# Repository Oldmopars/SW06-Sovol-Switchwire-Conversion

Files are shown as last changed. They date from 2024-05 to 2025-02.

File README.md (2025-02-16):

SV06 Switchwire Conversion Final Basic Enclosed
SV06 Switchwire Conversion Basic Open
SV06 Switchwire Conversion Full Monty
# SW06-Sovol-Switchwire-Conversion
Here it is. Until I can come up with a better name, I am calling it the SW06 (Switchwire/SV06). 
I had a few goals with this build. 
To reuse as many as possible of the original SV06 parts. At this point nearly all of the hard parts and electronics are being used, including the frame. Nearly all the plastic injection molded parts are replaced with printed parts. 
I wanted to make it better, faster and eliminate the Z banding issues. That is why the 		   CoreXZ. However, per the first goal, I am reusing the now unused X axis motor and putting it in the Y axis to have 2 Y axis motors. More power, and shorter belt path between motors. 
I wanted to be able to enclose it, but not require anything super complex to do so. I want to print ABS/ASA and other high temp filaments. This is one of the main reasons to base it off the Switchwire. Premade SW panel kit fits, it was designed around it. The only panel that will not fit is the deck panel, and it is now 3D printed in 6 parts to fit the SV06 print area. 
Easy upgrade path to an even better or faster machine. All of the Voron compatible toolheads including the Stealth Burner, XOL2, Dragon Burner, etc. will fit this now as it uses the Voron Mount system. This also means you can use TAP R8, CNC Tap, Beacon, Eddy, Klicky, etc. 
A budget to fit any wallet. There are 3 main options. First one is the Basic. This uses the stock 8mm Rods and LM8UU bearings in the Z, only requires 1 MGN12 linear rail. You will also need some F695 bearings, new belts and some hardware. If you do not have a RPi or some other Klipper screen, you will need that to convert to Klipper. This will keep the spend under $100 and reuse the stock hot end. 
If you can afford more, the enclosure is next. This will be a bit under $100. So, the basic, plus enclosure will cost between $150-200. 
The Full Monty. Here you add the MGN12 rails in the Z axis to full SW configuration. Add a Voron Tool Head with any upgrades you want. Add your choice of Probe, LEDs, MIC6 bed, and maybe even MGN12 for the bed.  Want to add a filter? Heater? Camera? 48mm motors? 48V with TMC5160’s? Sky is the limit and many of the options from the Switchwire will directly work on this. 
 I am still cleaning up the CAD files. Due to using the Voron as a base, moving fasteners around has been a royal pain, so most of the fasteners are not shown. I will be working to add these all in, but it will take time. 
  If anyone would like to build a BETA version, let me know and I will share the files with you. I would love to have some others build it first and help me flush out any issues I may have overlooked. 
  I look forward to sharing this with you all and hope to see many of these printers converted and doing great things. 

Please keep in mind that this is a ALPHA. I have yet to convert a full printer and so much of this is untested. Please feel free to use these files and let me know if anything needs to be fixed or changed. I would love to get feedback and see your builds. 

May 9 2024
I have updated the file. I have added the missing hardware and made some other changes. Please let me know if you find any issue with it. 

Feb 15 2025
I made some major upgrades to the X and Z motor mounts. It is now using the original Voron Switchwire motor mounts. This makes maintenace much easier. Prior version was difficult to change belt tension, or any other work on the motors. Now it is much easier to work on.

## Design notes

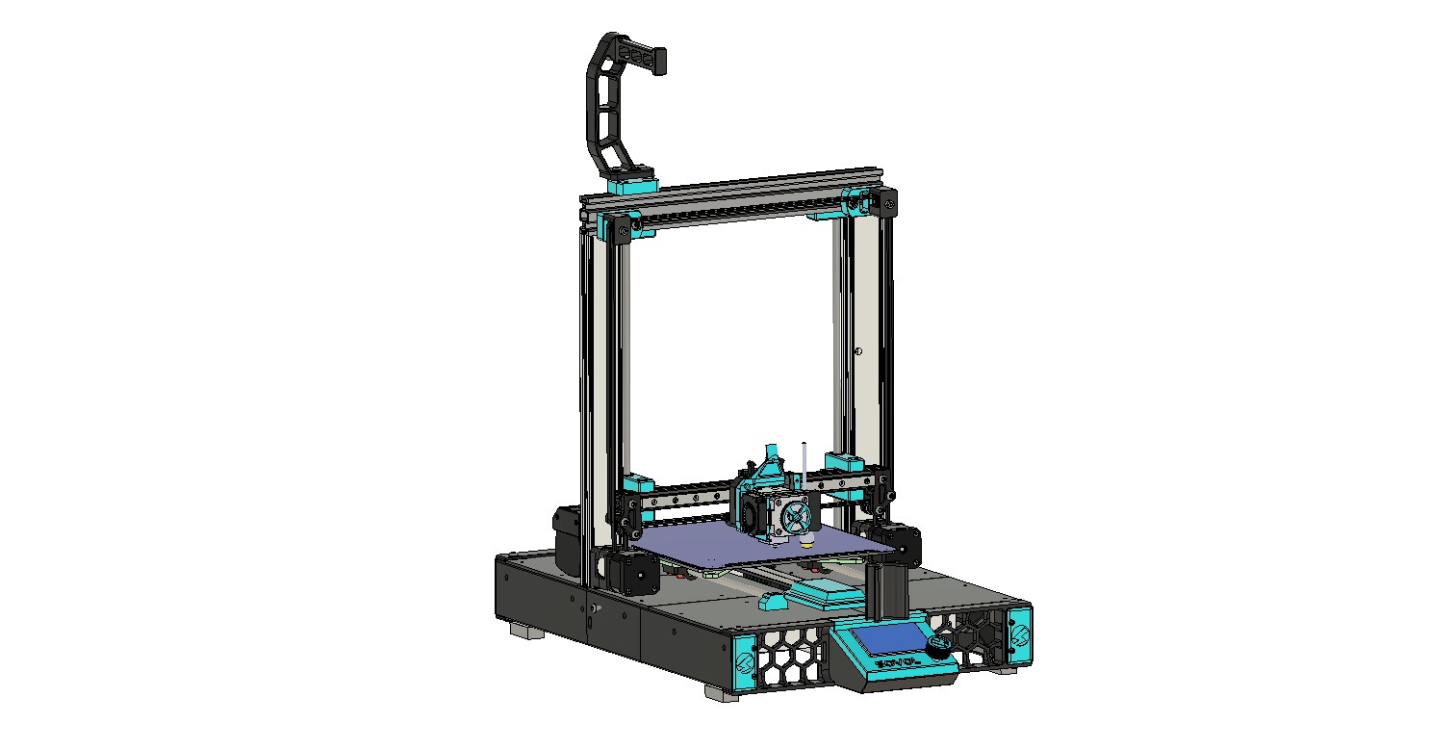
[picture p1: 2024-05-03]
SV06 Switchwire Conversion Basic Open.png

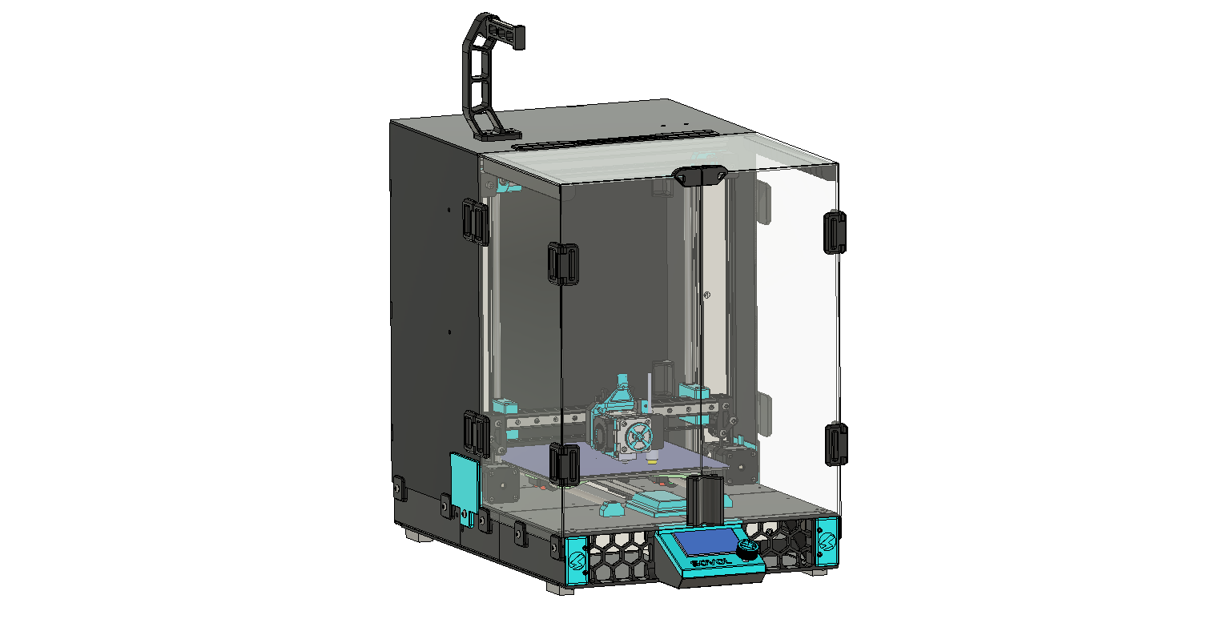
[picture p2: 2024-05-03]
SV06 Switchwire Conversion Final Basic Enclosed.png

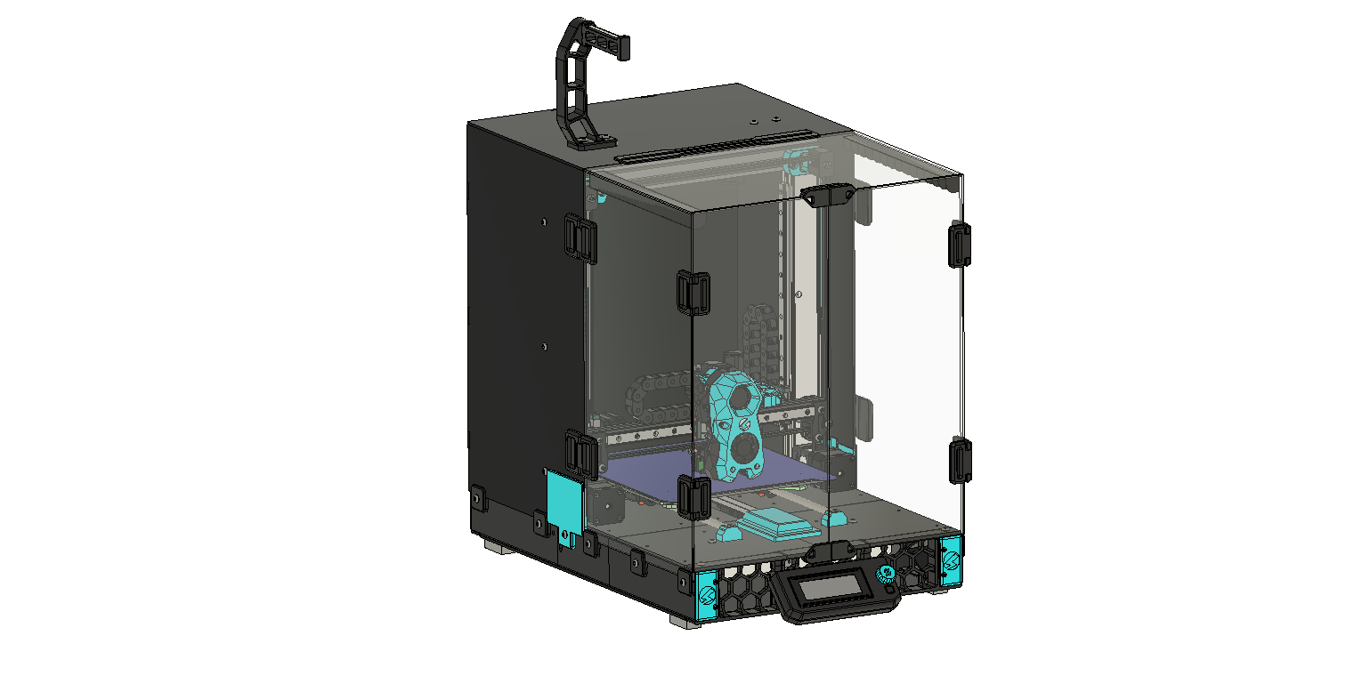
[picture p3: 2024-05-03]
SV06 Switchwire Conversion Full Monty.png

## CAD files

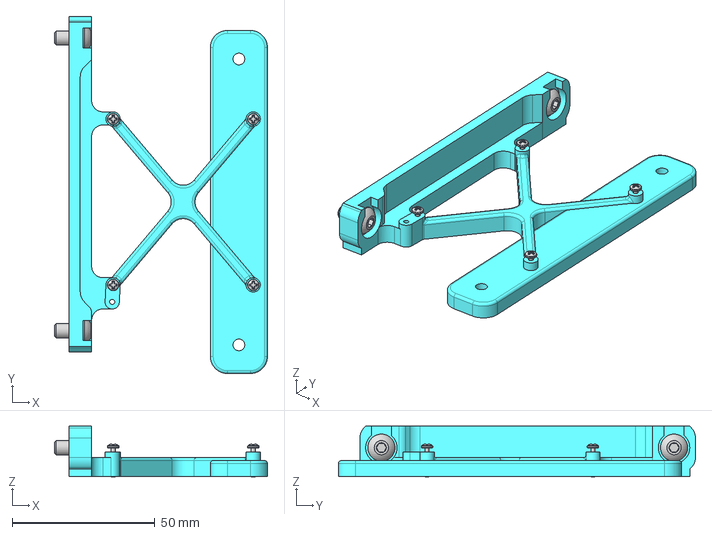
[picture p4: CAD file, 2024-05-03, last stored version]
SV06 Switchwire Conversion v7.step
74.5 x 124.9 x 17.7 mm
M5x10 BHCS (13) x 2
M2x10 SCREW x 4

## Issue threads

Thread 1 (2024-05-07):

Incomplete STEP

tt1pjm, 2024-05-07:
Not sure if it's intentional but the step only contains the RPi mount. Would be great to see the full model.

Oldmopars, 2024-05-07:
Sorry, fixing that now

Oldmopars, 2024-05-07:
OK, should be good now

Closed 2024-05-07.

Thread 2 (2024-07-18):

Patiently awaiting STEP

yamsinacan, 2024-07-18:
Hi Oldmopars, great project!

I'm looking to build and test the Basic-Open, saw the latest STEP was deleted but not replaced. Unsure if this is intentional but I'm excited to get a BOM.

Many thanks in advance!

yamsinacan, 2024-07-23:
I am silly, pulled STEP v30. Thank you!

yamsinacan, 2024-07-23:
Fingers crossed you manage to resolve things, v30 is in a beautiful place!

Many thanks for your project!

tt1pjm, 2024-07-24:
> Sorry I have not replied earlier. I have been working on this and I do have an updated STEP file, but it is too large and GitHub will not let me post it. So I am working to reduce the size, but every time I try my Fusion 360 locks up or crashes. Still working on a solution. Classified as Hypertherm Inc. - Business Use - This document contains information that is proprietary or confidential to Hypertherm, Inc.
> […](#)
> ________________________________ From: yamsinacan ***@***.***> Sent: Monday, July 22, 2024 8:34 PM To: Oldmopars/SW06-Sovol-Switchwire-Conversion ***@***.***> Cc: Subscribed ***@***.***> Subject: Re: [Oldmopars/SW06-Sovol-Switchwire-Conversion] Patiently awaiting STEP (Issue #2) I am silly, pulled STEP v30. Thank you! — Reply to this email directly, view it on GitHub<[#2 (comment)](https://github.com/Oldmopars/SW06-Sovol-Switchwire-Conversion/issues/2#issuecomment-2244184224)>, or unsubscribe<https://github.com/notifications/unsubscribe-auth/A7UR6JKQOXSIDLRJ4BQH3JDZNXFLPAVCNFSM6AAAAABLDN5PN2VHI2DSMVQWIX3LMV43OSLTON2WKQ3PNVWWK3TUHMZDENBUGE4DIMRSGQ>. You are receiving this because you are subscribed to this thread.Message ID: ***@***.***>

Hey Oldmopars!

I'm looking forward to building this soon.
You can upload much larger files by creating a release and attaching it there. (if your file size is >25mb and <100mb you can also use command line). Hope that helps.

Oldmopars, 2024-07-24:
I was finally able to get the latest version to upload. Enjoy

Classified as Hypertherm Inc. - Business Use - This document contains information that is proprietary or confidential to Hypertherm, Inc.

________________________________
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

yamsinacan, 2024-07-30:
Very many thanks Oldmopars, amazing work!

Just a quick question but I was unsure where best to ask, and there's absolutely no rush on response! With the stock toolhead and linear rod system, can you confirm the lengths of the required extrusion and linear rail for the X-axis?

Listed dimensions are as follows, but these do not allow for the printed parts "XZ Block - Left/Right" to fit squarely on the extrusion, each overhanging by 5mm due to the rail. Unsure if this is intended or if adjustments are needed so I thought I'd ask, but I assume it simply requires a 270mm rail.

315mm 2020 extrusion
280mm MGN12 linear rail

Closed 2024-07-23.

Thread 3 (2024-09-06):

Some questions about the project

Reubertt, 2024-09-06:
I found the project very interesting, I analyzed some parts and I asked myself a few questions.

Why move the front plate away with a 3D model? I imagine it is to compensate for the hotend's distance, but since you are raising the Y axis supports, wouldn't it be better to just create them in an L shape and keep the entire gantry intact?

Another thing, I didn't quite understand how the Y belt tensioning works, does it move the entire second motor to do the tensioning?

And lastly, a while ago I changed the position of the cables on my bed to install a cable guide, I think something like that could be interesting for the project too.

Reubertt, 2024-09-12:
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

I believe a 20x60 aluminum profile with a linear axis in the middle could be good too, since it takes advantage of the holes in the front and rear plates and perhaps gives even more stability to the Y axis.

Oldmopars, 2024-09-14:
So, there were a few goals with this project. The biggest one was to reuse as many of the original SV06 parts as possible. I also wanted to limit the extra parts required to a minimum. The idea was to keep cost low.

The reason I didn't use an L style bracket and used printed parts to extend the frame was to keep it as rigid as possible. The L brackets would induce flex.

I am by no means an engineer, not even close and I don't promise to have all the answers. However, I have had my SW06 printing now for several months and it is rock solid and prints great. I am at the stage with it, that I know I can start working on making it go faster, but as it is, it prints so good, I hate to mess with it. And, for the record, I am only running one Y axis motor right now, I was having issues that turned out to be a bad motor, but it prints great with just one, so I left it.

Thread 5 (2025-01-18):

Starting project

Endl3ss721, 2025-01-18:
Hi!
   I would like to start building the switchwire conversion. I am new to GitHub and was unsure of the best way to contact you to get the files to get started.

Oldmopars, 2025-01-18:
I would be more than happy to share the files with you. As I am writing this I have parts running on my SW06. The files I have are what I would classify as rough Beta. Everything works, but there may be some tweaks that need to happen along the way. Not every screw and nut are called out, I don't have a ready made config that is plug and play. I am running a Pi4B with a BTT SKR E3 V3 and a BTT HDMI5. I am currently running with only one Y motor, but it can be run with 2. I need to buy 2 matching motors to get that to work and I just have not made it a priority. It is one of 7 Vorons I have and my attention is scattered.
So, I would be happy to send you the F3D (Fusion) files if you want them. I do not have them broken out into ready to print STLs yet.

Classified as Hypertherm Inc. - Business Use - This document contains information that is proprietary or confidential to Hypertherm, Inc.

________________________________
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

Endl3ss721, 2025-01-18:
The fusion files would be great! My sv06 is running the klipper screen you can get from sovol as the upgrade. Otherwise it's stock.

Closed 2025-01-19.

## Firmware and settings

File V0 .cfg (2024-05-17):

[include mainsail.cfg]
# This file contains common pin mappings for the BIGTREETECH SKR mini
# E3 v3.0. To use this config, the firmware should be compiled for the
# STM32G0B1 with a "8KiB bootloader" and USB communication.

# The "make flash" command does not work on the SKR mini E3. Instead,
# after running "make", copy the generated "out/klipper.bin" file to a
# file named "firmware.bin" on an SD card and then restart the SKR
# mini E3 with that SD card.

## Voron Design VORON 0.2 SKR Mini E3 V3 config

## *** THINGS TO CHANGE/CHECK: ***
## MCU path                                                                     [mcu] section
## Z and Extruder motor currents                                                [tmc2209 stepper_*] sections. Uncomment the stepper motor you have
## Full steps per rotation for Extruder                                         [extruder] section
## Thermistor types                                                             [extruder] and [heater_bed] sections - See https://www.klipper3d.org/Config_Reference.html#common-thermistors for common thermistor types
## Motor currents                                                               [extruder] [stepper] and {_HOME_X/Y] macro sections
## PID tune                                                                     [extruder] and [heater_bed] sections
## Fine tune E steps                                                            [extruder] section
## For more info                                                                check https://docs.vorondesign.com/build/startup/#v0

[mcu]
#####################################################################
# Obtain definition by "ls -l /dev/serial/by-id/"
#####################################################################
serial: /dev/serial/by-id/usb-Klipper_stm32g0b1xx_4C0033001150415833323520-if00

[temperature_sensor mcu_temp]
sensor_type: temperature_mcu
min_temp: 0
max_temp: 100

[temperature_sensor host_temp]
sensor_type: temperature_host
min_temp: 10
max_temp: 100

[printer]
kinematics: corexy
max_velocity: 200
max_accel: 2000
max_z_velocity: 15
max_z_accel: 300
square_corner_velocity: 6.0

#####################################################################
#      X/Y Stepper Settings
#####################################################################

[stepper_x]
step_pin: PB13
## Refer to https://docs.vorondesign.com/build/startup/#v0
dir_pin: PB12                                                       # Check motor direction in link above. If inverted, add a ! before PB12
enable_pin: !PB14
rotation_distance: 40
microsteps: 32
full_steps_per_rotation: 200                                        # Set to 400 for 0.9° degree stepper motor, 200 is for 1.8° stepper motors
endstop_pin: tmc2209_stepper_x:virtual_endstop 
position_endstop: 119
position_max: 120
homing_speed: 20                                                    # for sensorless homing it is recommended not to go above 40mm/s   
homing_retract_dist: 0

[tmc2209 stepper_x]
uart_pin: PC11
tx_pin: PC10
uart_address: 0
interpolate: False
run_current: 0.7           
# you need to calculate the run_current value using the equation (rated_motor_current * 0.707 = Maximum_run_current) start with a value that is about 60%-70% of your maximum value.
sense_resistor: 0.110
stealthchop_threshold: 0                                            # Set to 999999 to turn stealthchop on, and 0 to use spreadcycle
diag_pin: ^PC0  													# YOU NEED TO JUMP THIS DIAG PIN ON YOUR BOARD FOR SENSORLESS HOMING TO WORK 
driver_SGTHRS: 70                                                 # this is set to 255 which is the MAX sensitivity for sensorless homing, you will need to tune this later

[stepper_y]
step_pin: PB10
## Refer to https://docs.vorondesign.com/build/startup/#v0
dir_pin: PB2                                                        # Check motor direction in link above. If inverted, add a ! before PB2
enable_pin: !PB11
rotation_distance: 40
microsteps: 32
full_steps_per_rotation: 200                                        # Set to 400 for 0.9° degree stepper motor, 200 is for 1.8° stepper motors
endstop_pin: tmc2209_stepper_y:virtual_endstop
position_endstop: 118
position_max: 120
homing_speed: 20                                                    # for sensorless homing it is recommended not to go above 40mm/s   
homing_retract_dist: 0
homing_positive_dir: true

[tmc2209 stepper_y]
uart_pin: PC11
tx_pin: PC10
uart_address: 2
interpolate: False
run_current: 0.7           
# you need to calculate the run_current value using the equation (rated_motor_current * 0.707 = Maximum_run_current) start with a value that is about 60%-70% of your maximum value.
sense_resistor: 0.110
stealthchop_threshold: 0                                            # Set to 999999 to turn stealthchop on, and 0 to use spreadcycle
diag_pin: ^PC1   												    # YOU NEED TO JUMP THIS DIAG PIN ON YOUR BOARD FOR SENSORLESS HOMING TO WORK
driver_SGTHRS: 75                                               # this is set to 255 which is the MAX sensitivity for sensorless homing, you will need to tune this later

#####################################################################
#   Z Stepper Settings
#####################################################################

[stepper_z]
step_pin: PB0
dir_pin: !PC5                                                       # Remove the ! before PC5 if motor direction is inverted.
enable_pin: !PB1
rotation_distance: 8                                                # For T8x8 integrated lead screw
microsteps: 32
endstop_pin: ^PC2
#position_endstop: 125
position_max: 125
position_min: -4
homing_speed: 20
second_homing_speed: 3.0
homing_retract_dist: 3.0

[tmc2209 stepper_z]
uart_pin: PC11
tx_pin: PC10
uart_address: 1
interpolate: False
## For OMC (StepperOnline) 17LS13-0404E-200G 0.4A 
run_current: 0.5
## For LDO-42STH25-1004CL200E 1.0A
#run_current: 0.37
sense_resistor: 0.110
stealthchop_threshold: 0                                            # Set to 999999 to turn stealthchop on, and 0 to use spreadcycle

#####################################################################
#   Extruder
#####################################################################

[extruder]
step_pin: PB3
dir_pin: !PB4                                                        # Add ! if moving opposite direction
enable_pin: !PD1
full_steps_per_rotation: 200                                       # Set to 200 for LDO 1.8° stepper motor, and set to 400 for OMC(StepperOnline) 0.9° stepper motor
rotation_distance: 22.23                                            # See calibrating rotation_distance on extruders doc
gear_ratio: 50:10                                                   # For Mini Afterburner
microsteps: 32
nozzle_diameter: 0.400
filament_diameter: 1.750
heater_pin: PC8
## Check what thermistor type you have. See https://www.klipper3d.org/Config_Reference.html#common-thermistors for common thermistor types.
## Use "Generic 3950" for NTC 100k 3950 thermistors
sensor_type: Generic 3950
sensor_pin: PA0
control: pid                                                        # Do PID calibration after initial checks
pid_Kp: 28.182
pid_Ki: 1.978
pid_Kd: 100.397
min_temp: 0
max_temp: 270
min_extrude_temp: 170
max_extrude_only_distance: 150
max_extrude_cross_section: 1
pressure_advance: 0.02                                               # See tuning pressure advance doc
pressure_advance_smooth_time: 0.040

[tmc2209 extruder]
uart_pin: PC11
tx_pin: PC10
uart_address: 3
interpolate: False
## For OMC (StepperOnline) 14HR07-1004VRN 1A 0.9°
run_current: 0.5   # for OMC 14HR07-1004VRN rated at 1A
## For LDO LDO 36STH17-1004AHG 1A 1.8° 
#run_current: 0.3   # for LDO 36STH17-1004AHG
## For LDO LDO 36STH20-1004AHG 1A 1.8° 
#run_current: 0.6   # for LDO 36STH20-1004AHG
sense_resistor: 0.110
stealthchop_threshold: 0                                            # Set to 0 for spreadcycle, avoid using stealthchop on extruder

#####################################################################
#   Bed Heater
#####################################################################

[heater_bed]
heater_pin: PC9
## Check what thermistor type you have. See https://www.klipper3d.org/Config_Reference.html#common-thermistors for common thermistor types.
## Use "Generic 3950" for Keenovo heaters
sensor_type: Generic 3950
sensor_pin: PC4
smooth_time: 3.0
#max_power: 0.6                                                     # Only needed for 100w pads
min_temp: 0
max_temp: 120
control: pid                                                        # Do PID calibration after initial checks
pid_kp: 68.453
pid_ki: 2.749
pid_kd: 426.122

#####################################################################
#   Fan Control
#####################################################################
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

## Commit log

2024-05-07 Delete SV06 Switchwire Conversion v7.step
    removed
    [SV06 Switchwire Conversion v7.step]
2024-05-14 Minor file updates
    I found some holes to be the wrong size in the Y axis mount. Made minor changes to the Lower Rod Mounts for stock Rod Mounts
2024-05-17 Create V0 .cfg
    [V0 .cfg]
2024-05-18 Latest changes. Some holes fixed, Y axis relocated
    As I build this I am finding small errors that need correcting. Here it the latest version
2025-02-16 Delete SV06 Switchwire Conversion v48.step.zip
    Adding updated file
2025-02-16 Add files via upload
    Major update to the X and Z motor mounts
